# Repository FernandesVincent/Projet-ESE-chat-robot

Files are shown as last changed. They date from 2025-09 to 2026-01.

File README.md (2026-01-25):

# Projet ESE – Chat Robot  

Le projet de Chat Robot développé dans le cadre de la spécialité ESE dirigée par M.Fiack et supervisée par lui et M. Papazogou s'est achevé le vendredi 16 Janvier 2026. 

Nous allons donc revenir ici sur les différents aspects notables du projet, notamment ceux où notre projet s'est détaché des consignes initiales.

Nous allons donc passer en revue les différentes parties du projet en commençant par une partie sur l'organisation du projet et des tâches attribuées aux différents membres de l'équipe puis nous aborderons la partie Hardware séparée en deux sous parties, l'une pour la modélisation 3D sous Onshape et l'autre pour la conception de PCB sous Kicad. Puis, nous aborderons la partie Software séparée en plusieurs parties, chachune abordant un composant important du projet. 

Par soucis de lisibilité de l'ensemble du document nous n'allons pas détaillé en profondeur toutes les parties et sous parties liées à la mise en place de chaque composant sur le PCB ou à leur programmation. À la place, nous expliquerons brièvement l'ensemble des logiques hardware et software pour ensuite analyser en profondeurs seulement certains aspects de ces parties.

## Organisation du Projet

Le projet a été porté par une équipe de quatres étudiants de 3ème année à l'ENSEA faisant partit de la spécialité ESE, cette équipe est composée de : 

- Vincent FERNANDES
- Paul CAILLAUD
- Kelly LUO
- Yimei Xia

Après diverses discussions au cours du semestre, voici comment ont été attribués les rôles concernant le projet : 

- Vincent : PCB, modélisation/impression 3D, Soudure CMS & THT, TOFs, Moteurs, LED, LiDAR, mise en commun du code sous FreeRTOS
- Paul : Modélisation 3D, cablâge, Soudure CMS & THT, Accéléromètre, Moteurs
- Kelly : Lidar
- Yimei : Accéléromètre

Par ailleurs un README relatant l'avancée à mi-parcours (13 Novembre) est disponible dans le dossier Gestion.

## Hardware

### Modélisation 3D

Pour notre projet, nous avons décidés d'utiliser un pack de batteries Li-ion 2S au lieu du pack de 5 batteries NIMH fournit à la base car cela nous apporte une stabilité de maintient de la tension aux bornes de la batterie ainsi qu'une simplicité de la recharge. En effet, pour recharger les batteries que nous utilisions il nous fallait simplement les connecter à n'importe quelle alimentation stabilisée à 8.4V et non pas un chargeur dédié comme pour les batteries NIMH.

Cela étant, dû au fait d'avoir modifier les batteries nous avons dû adapter notre modélisation 3D. Nous avons donc décider d'inclure la pack de batteries directement dans la base du robot comme présenté ci-dessous afin d'augmenter la stabilité de l'ensemble. Cependant, cela a eu pour effet d'augmenter le diamètre de la base de notre robot passant d'une quinzaine de centrimètre à une vingtaine. De plus, nous avons ajouté un cache sur le dessus de la base pour bloquer la batterie en cas de chute ou autre accident. Finalement nous avons également équipé la base d'un arceau afin d'accueillir un bandeau de LED Neopixel ws2812b. 

<figure style="display:flex; gap:5px;">
  <figure style="text-align:center;">
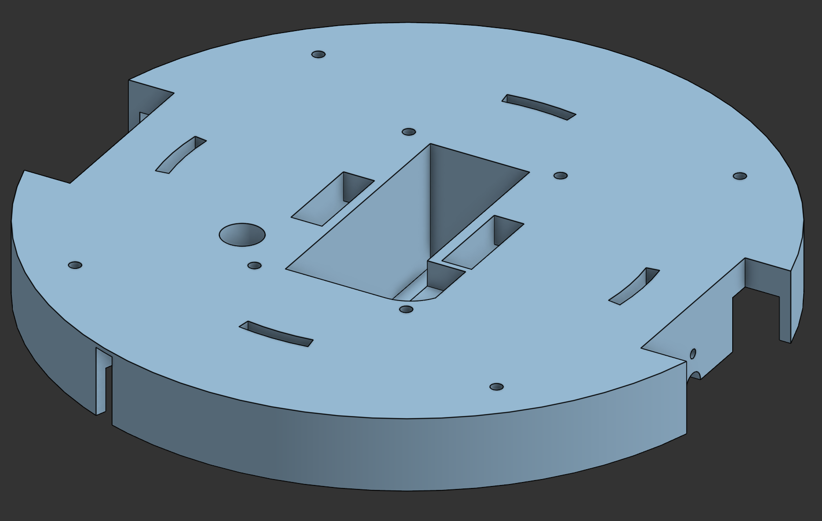
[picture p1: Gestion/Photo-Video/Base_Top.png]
    
    <figcaption>Base vue du dessus</figcaption>
  </figure>
  <figure style="text-align:center;">
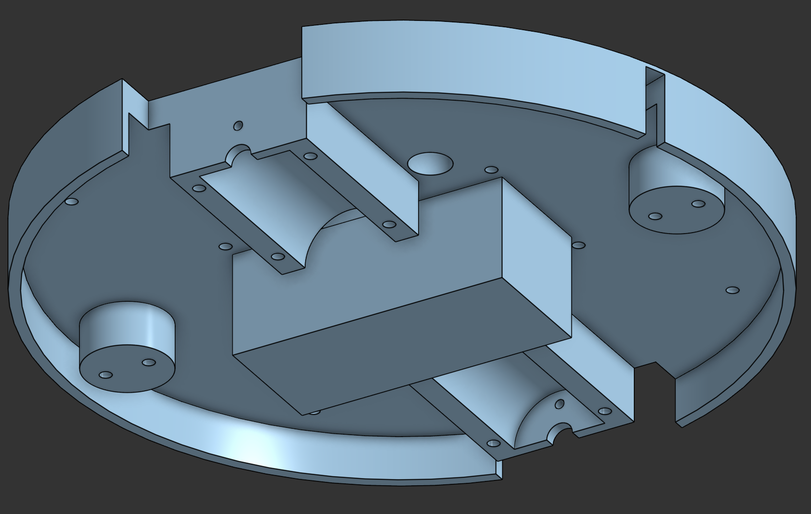
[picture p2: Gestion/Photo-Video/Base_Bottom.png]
    
    <figcaption>Base vue du dessous</figcaption>
  </figure>
</figure>
<figure style="display:flex; gap:5px;">
  <figure style="text-align:center;">
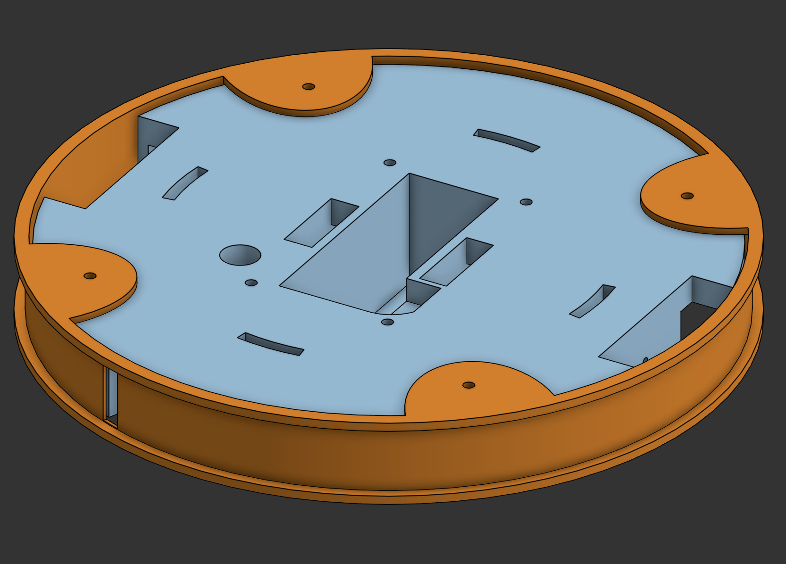
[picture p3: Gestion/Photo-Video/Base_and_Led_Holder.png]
    
    <figcaption>Support de LED</figcaption>
  </figure>
  <figure style="text-align:center;">
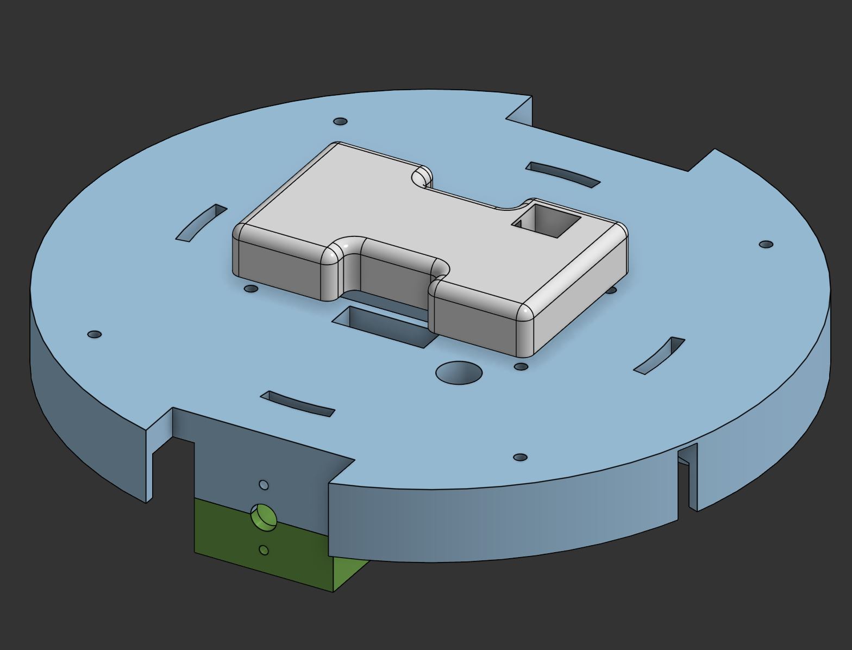
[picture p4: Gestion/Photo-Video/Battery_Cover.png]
    
    <figcaption>Cache de la batterie</figcaption>
  </figure>
</figure>

Contrairement aux autres robots, nous n'avons fait qu'un unique étage, sur lequel sont placé les 6 TOFs et le LiDAR, afin d'avoir la place entre le cache de la batterie et le sol de cet étage de placer le PCB suspendu par des vis M3 et bloqué par les écrous correspondants.

<figure style="display:flex; gap:16px;">
  <figure style="text-align:center;">
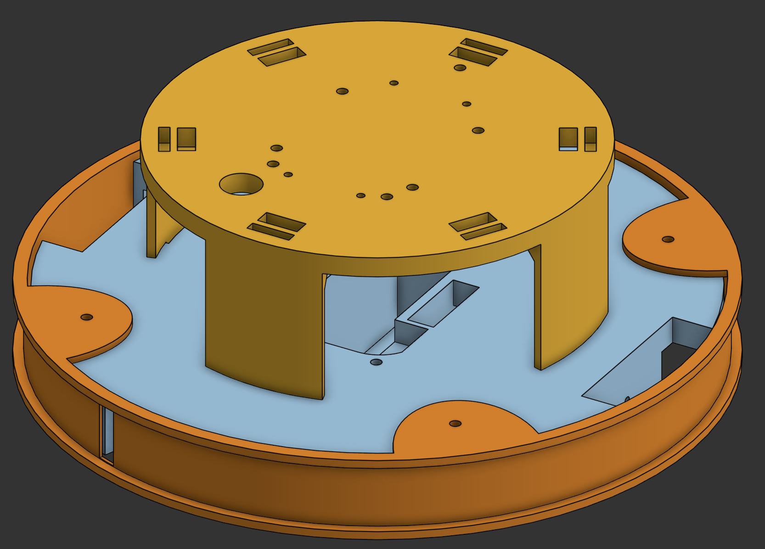
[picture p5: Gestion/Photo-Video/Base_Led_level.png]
    
    <figcaption>Étage du robot</figcaption>
  </figure>
  <figure style="text-align:center;">
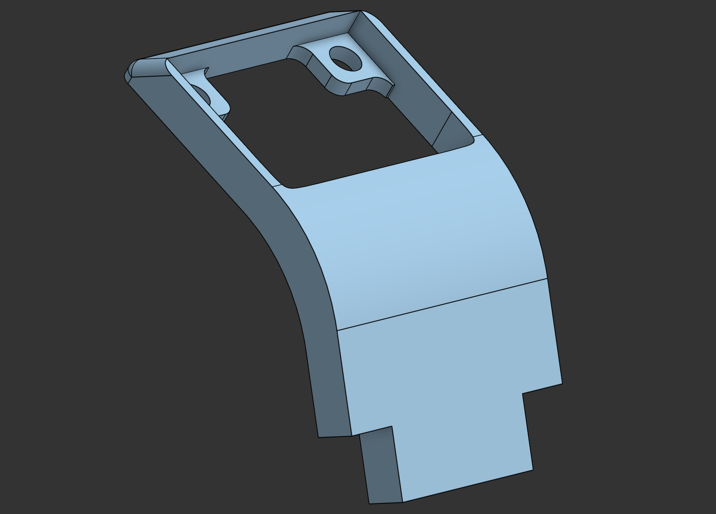
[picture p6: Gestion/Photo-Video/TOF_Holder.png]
    
    <figcaption>Support de TOF</figcaption>
  </figure>
</figure>

De plus, nous avons également modifier les roues afin d'y inclure non pas un mais deux joints toriques par roue afin, encore une fois, de garantir une meilleur stabilité du robot au vu de sa taille. Cependant, cela complexifie légèrement les virages que peut effectuer le robot là où les lignes droites sont cependant meilleures. 
De plus, pour équilibrer le robot nous utilisons des billes en métal dont le support initial accepte uniquement des vis M2 or nous n'avons pas réussi à trouver des vis de ce diamètre assez longues pour être compatible avec notre modélisation. Ainsi, nous avons recréés des supports inspirés des initiaux mais utilisant des vis M3 car nous les avions à la longueur adéquate et à cela s'ajoute qu'utiliser des vis de plus gros diamètre permet de joindre plus solidement les 2 pièces.

<figure style="display:flex; gap:16px;">
  <figure style="text-align:center">
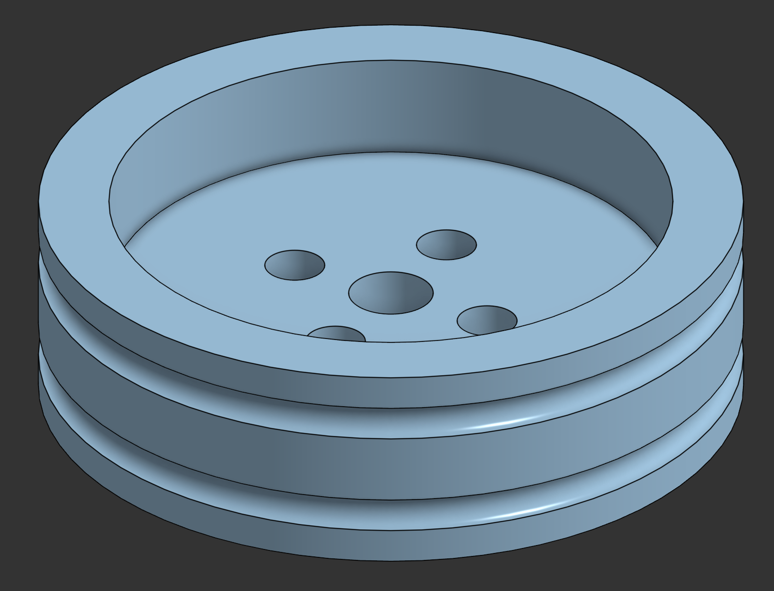
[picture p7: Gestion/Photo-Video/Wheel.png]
    
    <figcaption>Roue</figcaption>
  </figure>
  <figure style="text-align:center">
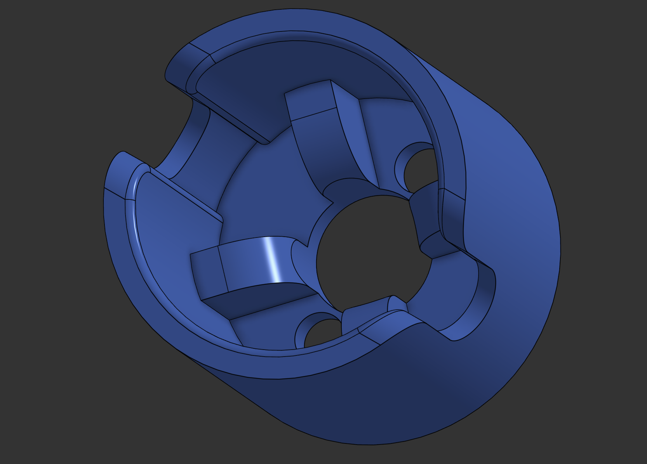
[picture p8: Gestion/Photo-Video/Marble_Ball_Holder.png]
    
    <figcaption>Support de bille</figcaption>
  </figure>
</figure>

### PCB

Pour la conception de PCB nous sommes passés par le logiciel KiCAD et nous en avons créés 4 différents pour certaines raisons que nous expliquerons au fur et à mesure de l'explication générale de chaque PCB.

#### PCB v1

Ce PCB est le premier qui a été designé pour le projet de robot chat. Il inclut notamment les composants de base utiles au bon fonctionnement du robot tel que les drivers de moteurs, l'accéléromètre et les connecteurs pour les TOFs ainsi que celui pour le LiDAR. En effet, pour ce projet nous avons choisis d'utiliser une solution à base de 6 TOFs afin de détecter le vide autour de la table sur laquelle se déplace le robot. Le choix de 6 TOFs a été réfléchis afin d'avoir suffisament de TOFs pour pouvoir repérer le vide peut importe l'orientation du robot au moment d'approcher le bord de table, sans non plus utiliser une quantité non raisonnable de capteurs.

De plus, ce PCB inclut trois nouveaux éléments que l'on a décidé d'ajouter à notre robot. Le premier est un connecteur vers un module MP3 dans le but de jouer un son, défini en amont, à certains moments clés de la présentation. On peut prendre comme exemple le moment où le vide est repéré par un TOF ou bien au moment d'une collision avec un autre robot. 

Le deuxième élément est un bandeau de LED Neopixels commandé par une PWM avec DMA. Le but ici est de venir, tout comme le module MP3, indiquer la réalisation de certaines actions du robot. Par exemple, l'idée principale était d'illuminer une des 96 LEDs du bandeau dès lors que le LiDAR détecte une cible. Certaines LEDs pourraient s'allumer en rouge en direction de cibles non valides alors qu'une LED unique serait allumée en direction de l'objet valide : l'autre robot.

Finalement, le troisième élément est une Raspberry Pi zéro 2W. Nous avons choisis de l'incorporer pour, d'une part, remplacer la connexion bluetooth demandée mais également d'une autre part pour y développer une interface graphique intéractive. Cette dernière permettrait de récupérer les données captées par le robot en temps réel mais également de lui envoyer des instructions, également en temps réel grâce à une lisaion UART.

L'ajout de ces composants nous a obligés à changer le microcontrôleur fourni de base par un STM32G474RET6 possédant, au contraire de l'initial, le nombre suffisant d'HUART accessibles simultanément pour nos besoins.

<figure style="display:flex; gap:16px;">
  <figure style="text-align:center">
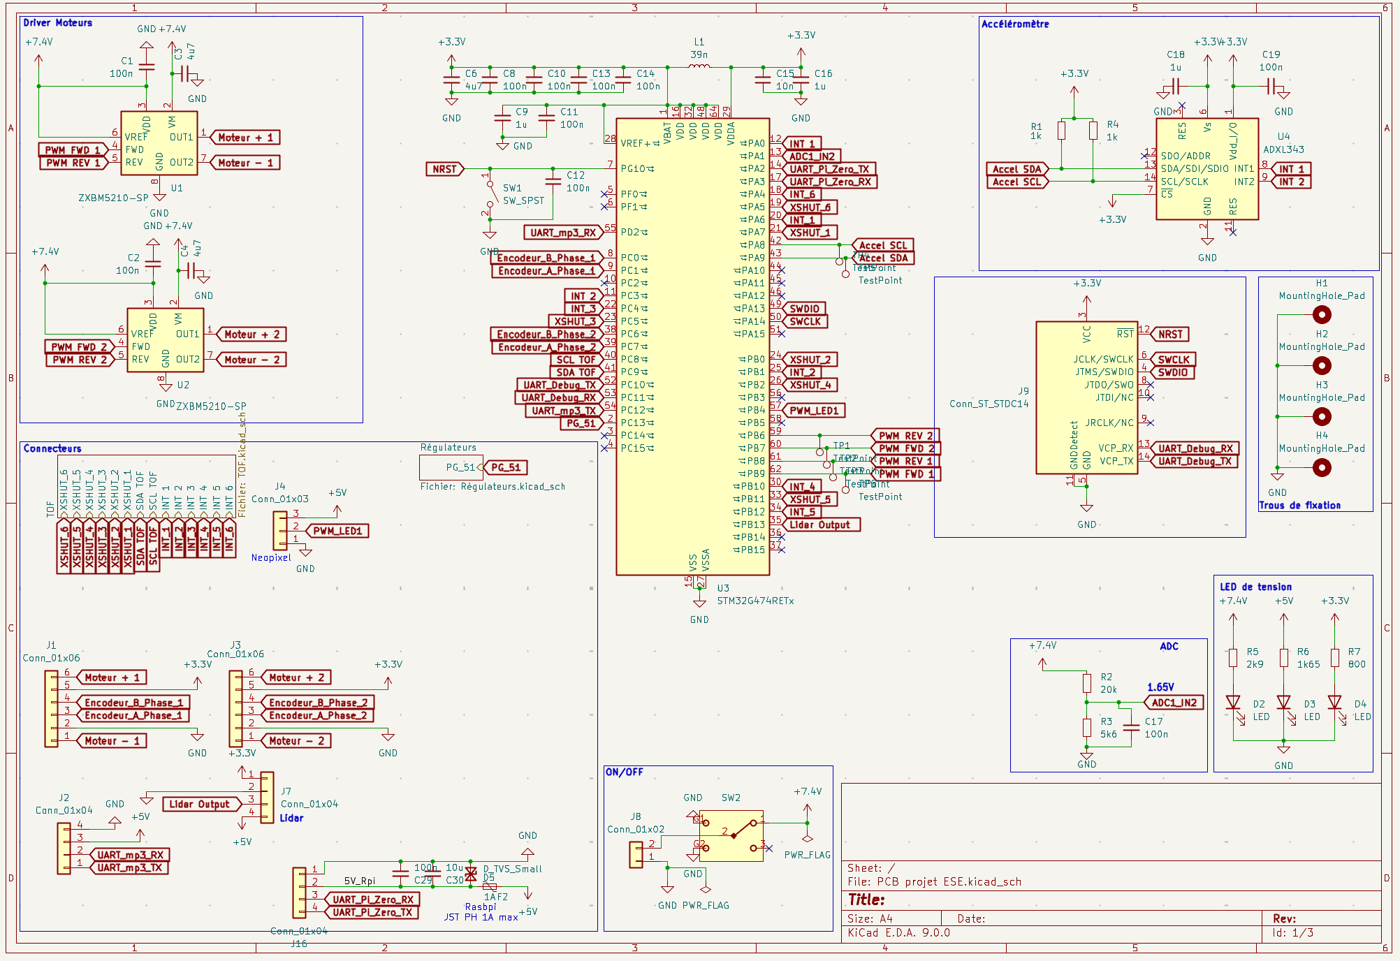
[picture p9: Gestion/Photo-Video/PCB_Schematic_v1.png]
    
    <figcaption>Schematic</figcaption>
  </figure>
  <figure style="text-align:center">
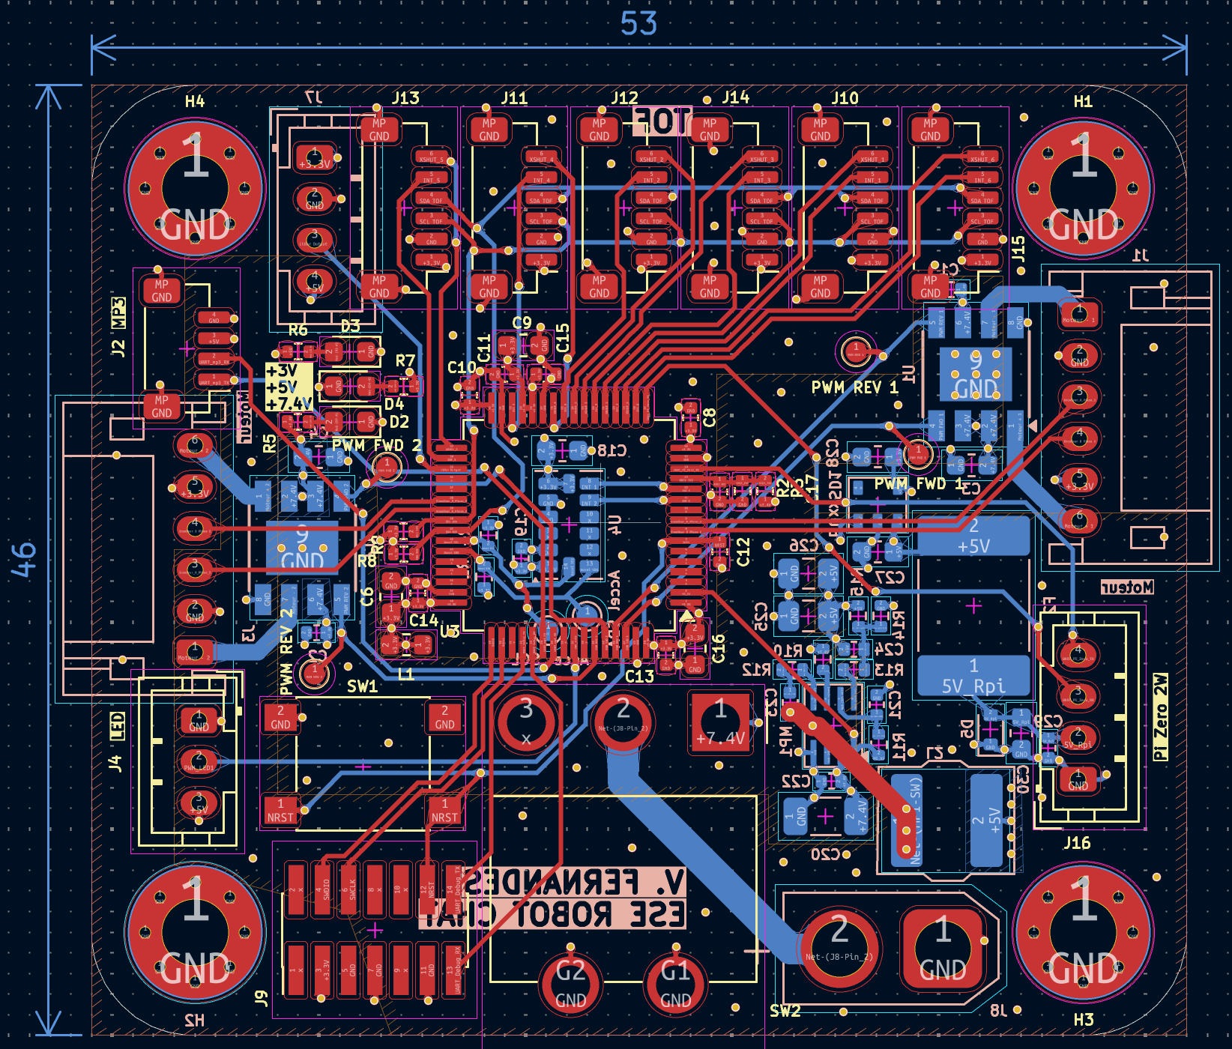
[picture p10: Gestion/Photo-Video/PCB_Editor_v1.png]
    
    <figcaption>PCB Editor</figcaption>
  </figure>
</figure>

Cependant, plusieurs problèmes datant de la conception sous KiCAD sont apparus une fois le PCB soudé et testé. Parmi celles-ci, les plus notables et plus importante sont les suivantes : 

- Oubli de connection de la pin ADDR de l'accéléromètre à GND (ou VCC en fonctiond de l'adresse voulue).
- Inversion des connexions SDA/SCL pour l'I2C de l'accéléromètre.
- Mauvaise connexion du pin Tx du LiDAR à un GPIO simple.
- Mauvaises connexions des pins GPIO des TOFs empêchant leur utilisation en interruption.

Même si, à la fin du projet nous avons pu en partie corriger ces erreurs de différentes façons il nous semblait essentiel de les faire apparaître dans ce compte rendu. Par exemple, nous avons connectés le LiDAR au connecteur de la Pi qui utilise également un UART et nous avons utilisés les TOFs en polling et non en interruption.

#### PCB v1.5

Cette version du PCB a été créée suite à la découverte des erreurs présentes sur la première version. Cette version a été designée dans l'idée d'avoir un PCB purement fonctionnel corrigeant les erreurs du PCB précédent tout en enlevant les éléments non nécessaires ajoutés dans la v1. Nous avons tout de même gardé le même microcontrôleur STM32G474RET6 bien que le nombre de pins soit bien plus important que nécessaire car cela nous a permis de gagné du temps en conception et le PCB a donc pu être réalisé en moins d'une journée.

<figure style="display:flex; gap:16px;">
  <figure style="text-align:center">
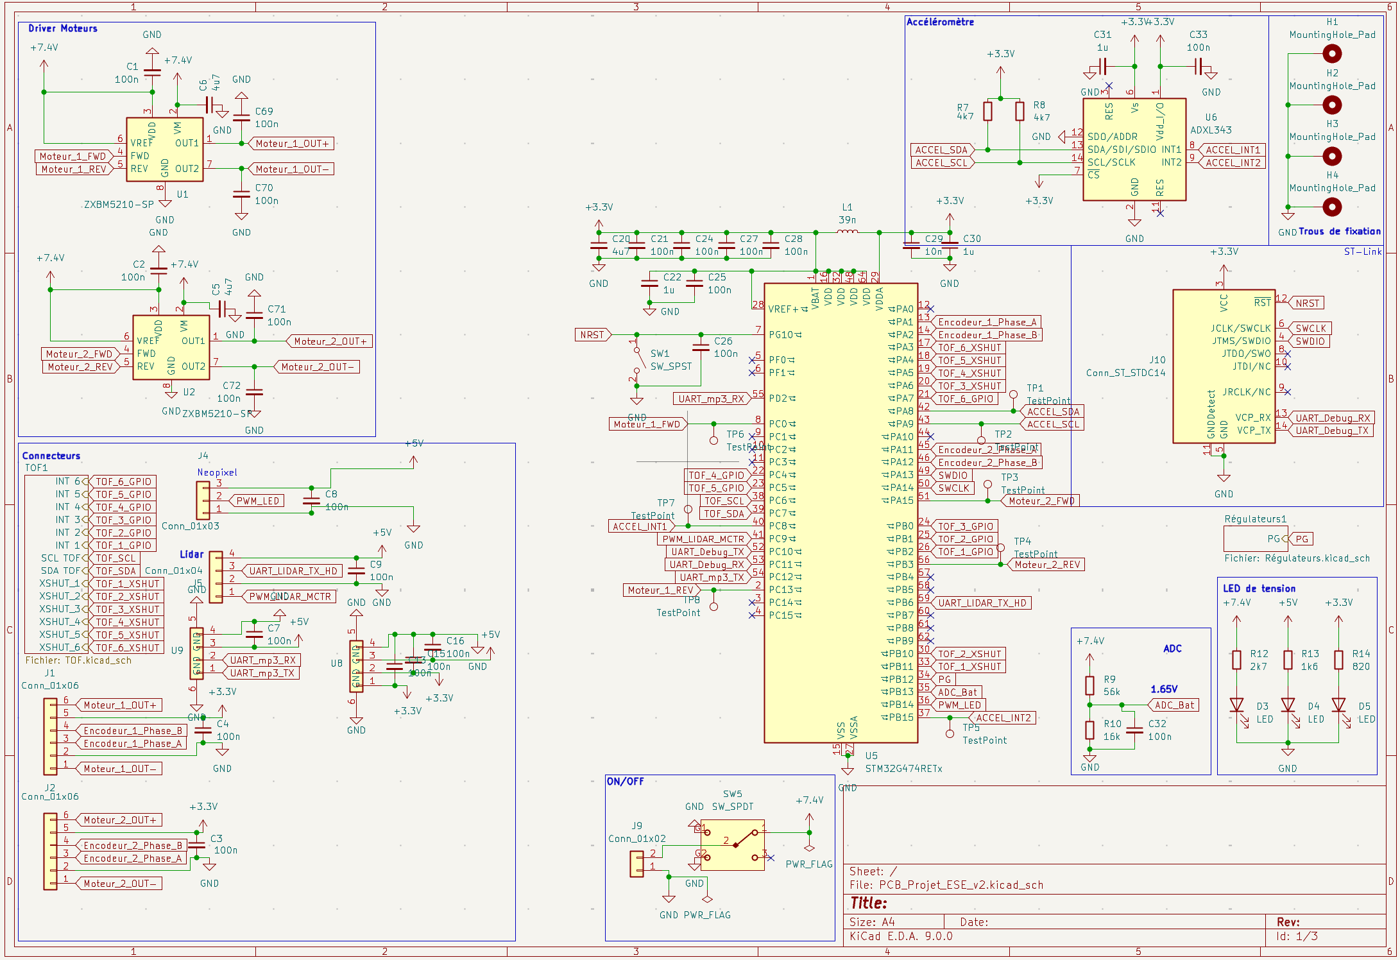
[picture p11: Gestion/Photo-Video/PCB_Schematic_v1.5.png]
    
    <figcaption>Schematic</figcaption>
  </figure>
  <figure style="text-align:center">
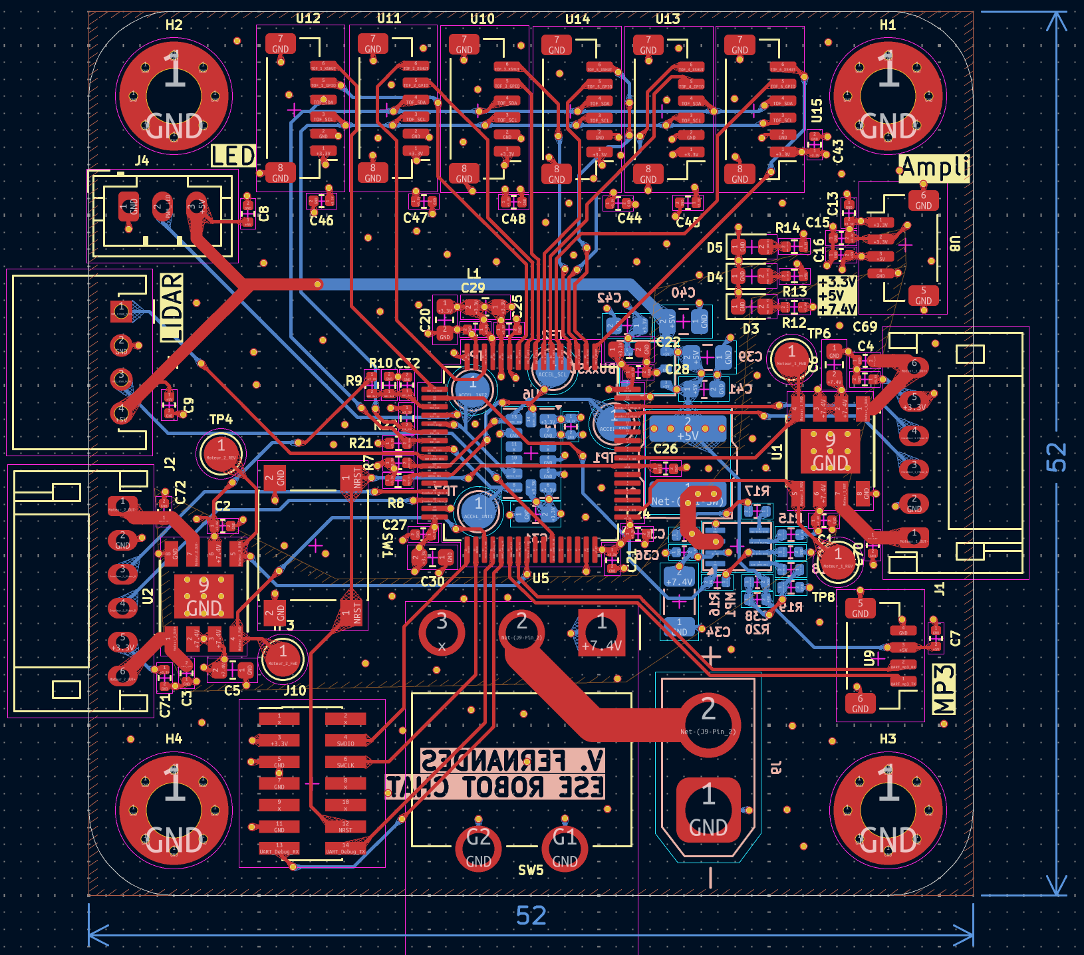
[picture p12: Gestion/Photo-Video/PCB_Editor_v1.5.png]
    
    <figcaption>PCB Editor</figcaption>
  </figure>
</figure>

Malheureusement, cette version a seulement eu le temps d'arrivée pour le jour exact de la présentation du projet car il y a eu de nombreuses semaines de retard dans la validation finale de la commande contenant ce PCB par le service déidé de l'établissement auprès du fabricant. 

#### PCB v2

Cette version est une version plus avancée du premier PCB, plus petite et comportant plus de composants et fonctionnalités. Parmi tout ces ajouts, les plus sont notables sont l'ajout d'un système de visualisation de la batterie en analogique uniquement, de résistances de shunt associées avec des amplificateurs afin de pouvoir asservir les moteurs en courant. De plus, des connecteurs pour utiliser pleinement le PCB dédié à l'amplificateur audio ainsi qu'un bouton ON-OFF-ON utilisé pour choisir le mode du robot ont été ajoutés au PCB.

<figure style="display:flex; gap:16px;">
  <figure style="text-align:center">
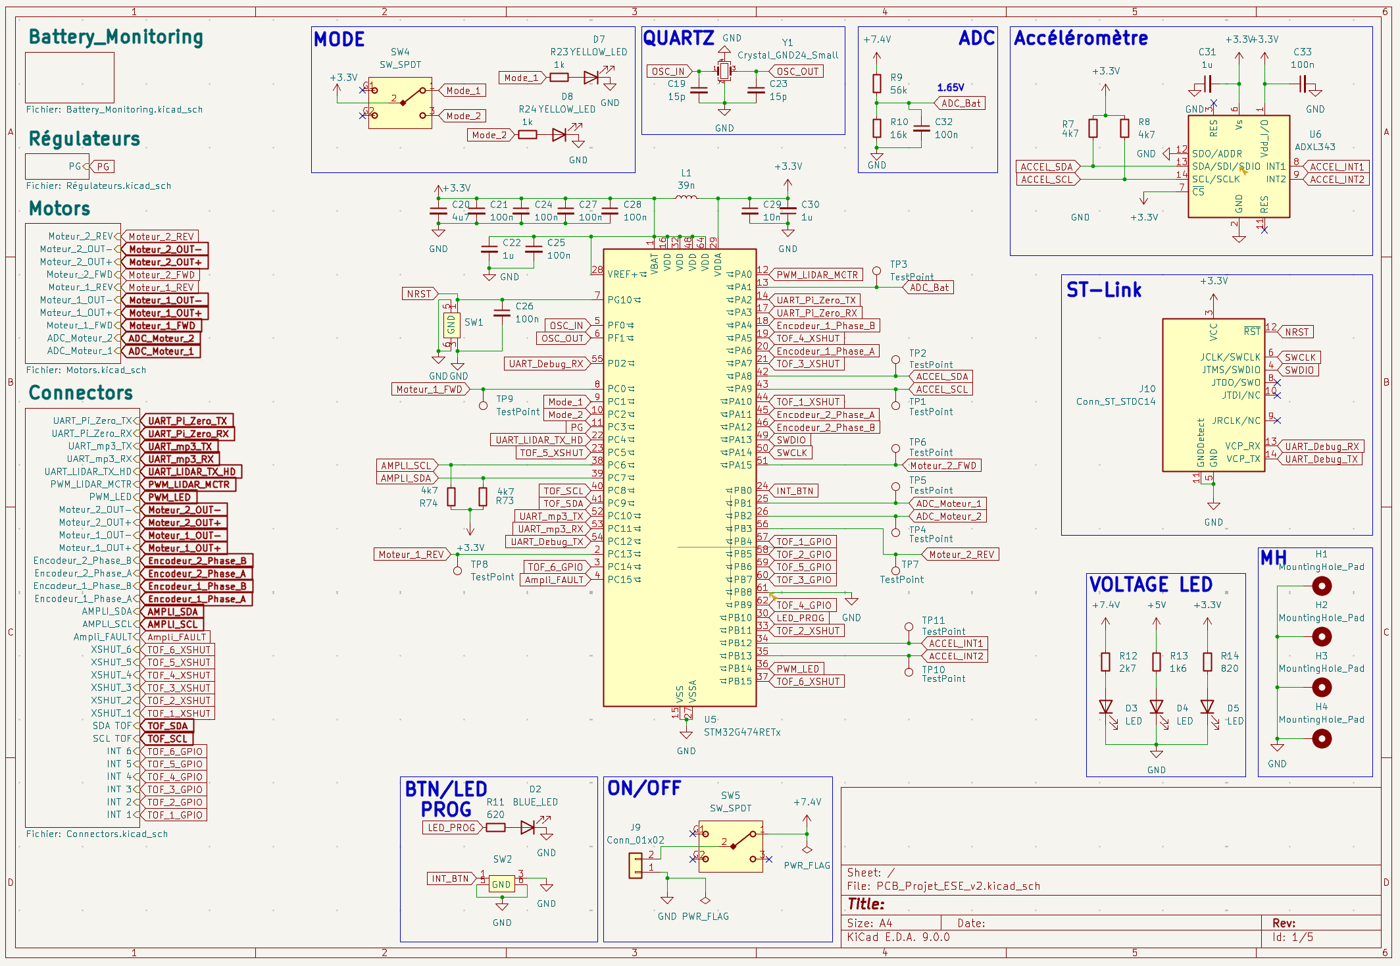
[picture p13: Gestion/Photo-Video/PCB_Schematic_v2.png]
    
    <figcaption>Schematic</figcaption>
  </figure>
</figure>

<figure style="display:flex; gap:16px;">
  <figure style="text-align:center">
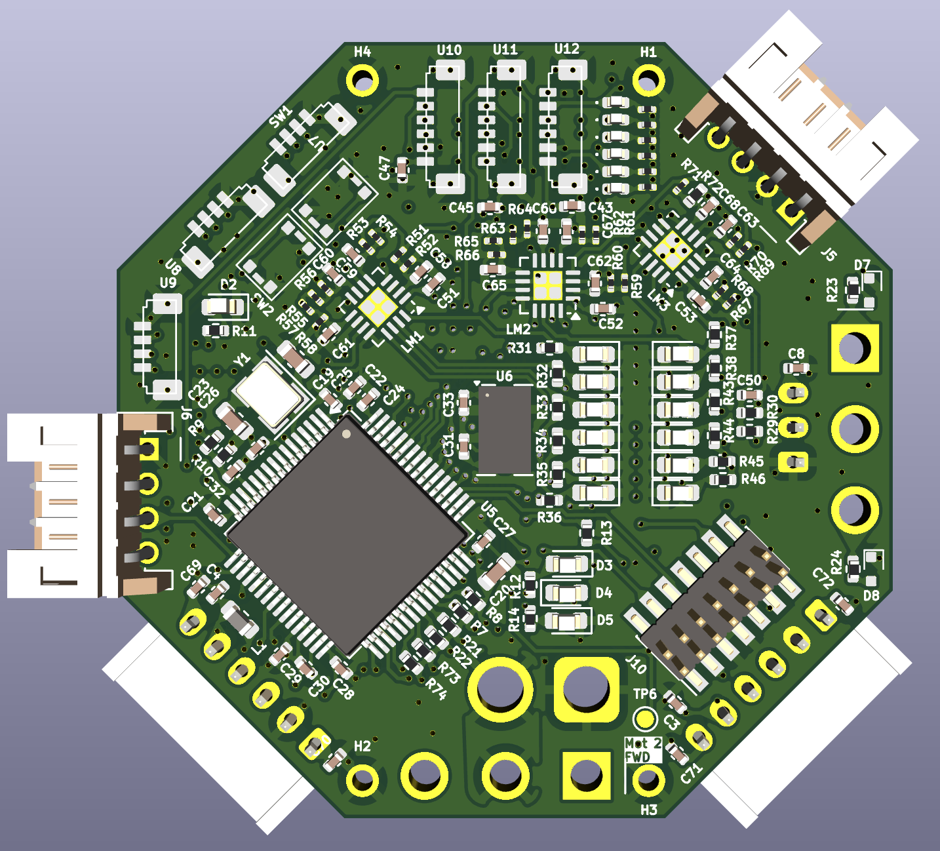
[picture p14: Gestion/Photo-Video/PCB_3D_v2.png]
    
    <figcaption>Vue 3D Top</figcaption>
  </figure>
  <figure style="text-align:center">
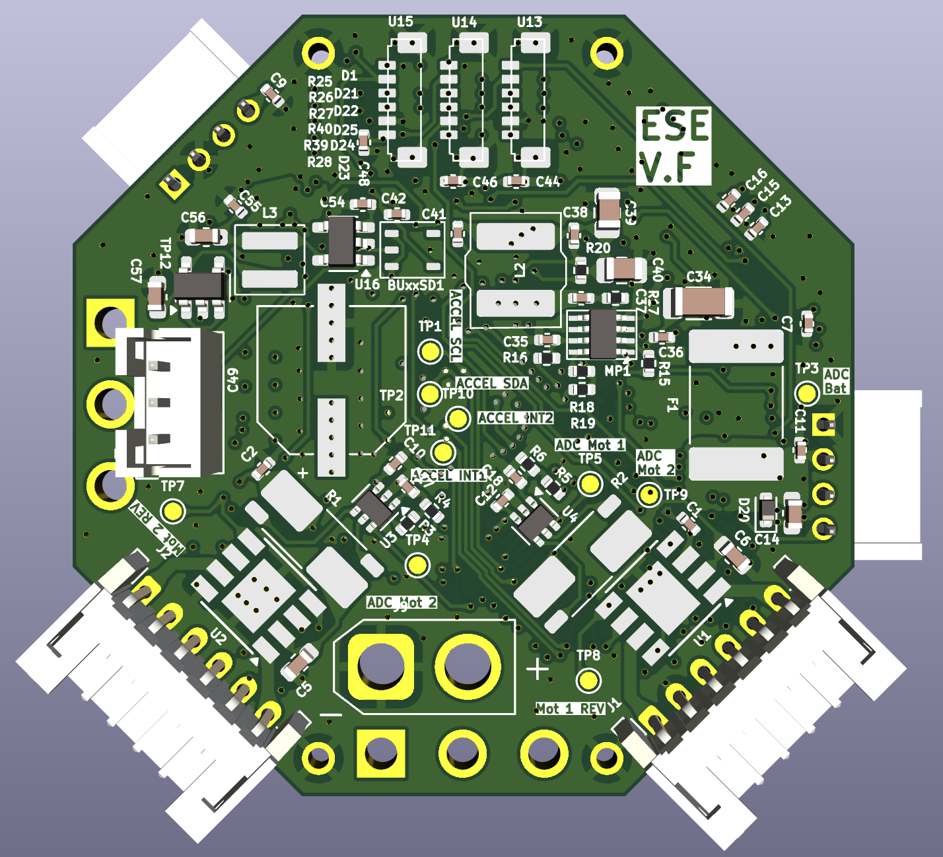
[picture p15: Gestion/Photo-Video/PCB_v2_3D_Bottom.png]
    
    <figcaption>Vue 3D Bottom</figcaption>
  </figure>
</figure>
  
Pour créer le système de surveillance de la batterie, des comparateurs LM339LVRTER ont été utilisés pour comparer la tension réelle de la batterie à une tension de référence qui ne varie pas même si la tension de la batterie diminue. Cette tension de référence a été créée par la mise en série d'un abaisseur de tension (MCP1802T-0902I/OT) permettant une sortie de tension de 0.9V tant que la tension d'entrée est supérieure à 2V et d'un amplificateur de tension (TPS61097A-33DBVR) permettant de ramener la tension à 3.3V qui est donc comparable à la tension réelle passée dans un diviseur de tension. Un module Buck-Boost aurait pu remplacer cette mise en série des deux composants mais nous n'en avons pas trouver permettant d'avoir ces valeurs de tension de manière stable même lorsque la tension réelle approche les 2V. 
Pour afficher le niveau de la batterie un jeu de 12 LEDs CMS a été installé sur le PCB, tant que la tension réelle est supérieure à la tension seuille, la LED associée est allumée mais dès lors que le tension réelle est inférieure à la tension seuille la LED s'éteint. Dans un soucis uniquement visuel les 12 LEDs forment un dégradé allant de vert à rouge.

Malheureusement, cette version a seulement pu être soudée (non testée) avant la présentation du projet car il y a eu de nombreuses semaines de retard dans la validation finale de la commande contenant ce PCB par le service déidé de l'établissement auprès du fabricant. 

#### PCB audio

Ce PCB très simple utilise uniquement un amplificateur audio (LM48100QMHX/NOPB) afin d'amplifier le signal en sortie du module MP3. Ce dernier utilise un câble mini-jack fonctionnant pour une utilisation en connexion directe comme avec un casque audio. Cependant cette sortie mini-jack ne fournit pas assez de puissance pour qu'un haut parleur directement connecté à celle-ci produise un son audible. Il faut donc, entre le haut-parleur et le module MP3, ajouter un amplificateur audio. 

<figure style="display:flex; gap:16px;">
  <figure style="text-align:center">
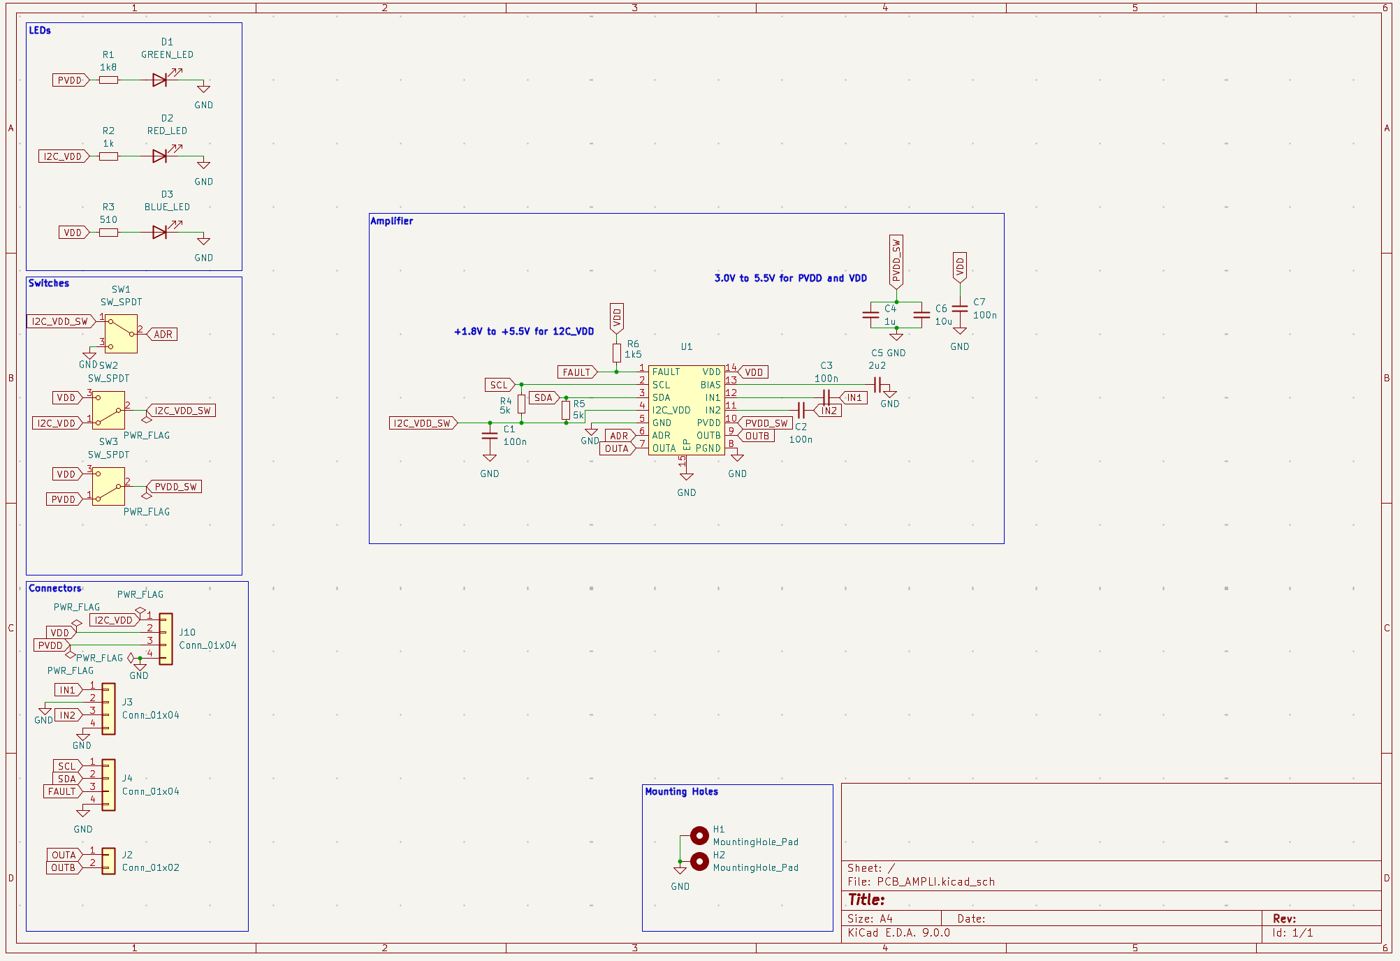
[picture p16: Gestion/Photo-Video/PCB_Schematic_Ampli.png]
    
    <figcaption>Schematic</figcaption>
  </figure>
  <figure style="text-align:center">
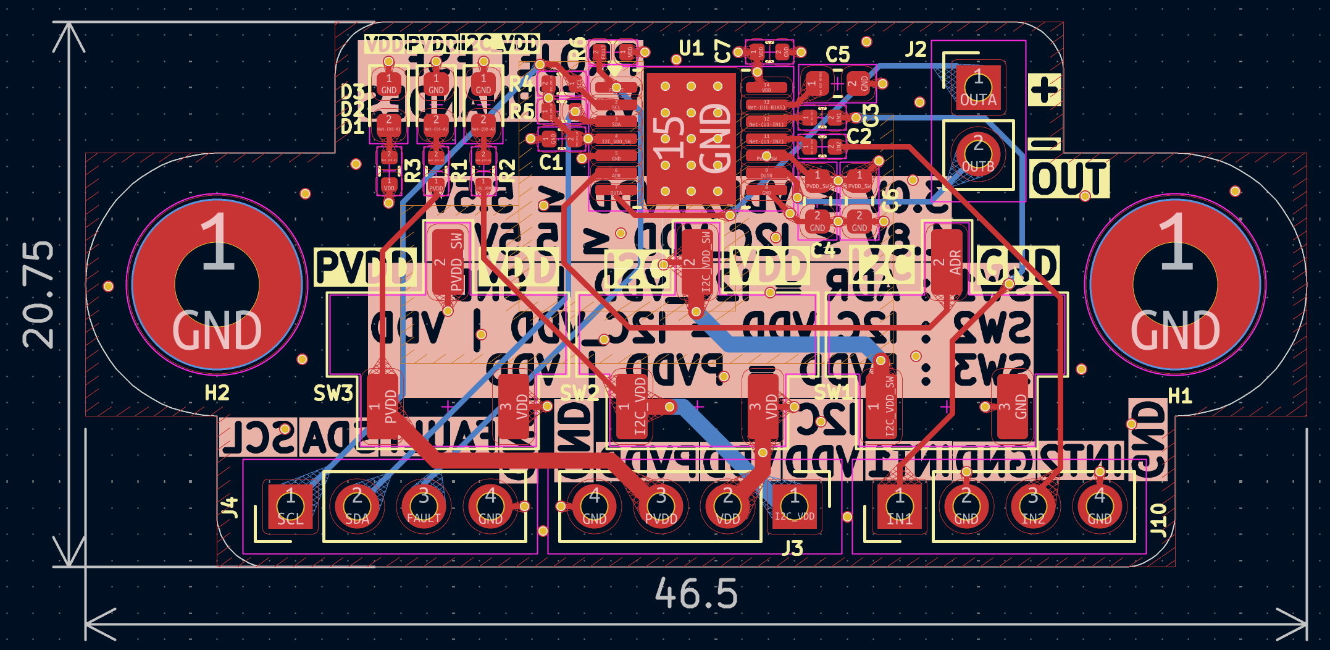
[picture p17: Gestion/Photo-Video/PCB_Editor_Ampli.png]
    
    <figcaption>PCB Editor</figcaption>
  </figure>
</figure>

Cet amplificateur audio a été choisi, tout d'abord pour ses spécificités techniques de 1W/8ohms correspondant excatement à celles de notre haut-parleur. De plus, quand la liste des choix possibles a été suffisament réduite nous avons pris le parti de choisir celui de la marque Texas Instrument car leur documentation est très lisible et compréhensible comparée à celle de leur concurrent. Cela nous permet, par exemple, de réduire le temps passé tant sur la partie hardware que sur la partie software de ce PCB. De plus, La communication I2C de cet l'amplificateur permet de modifier le volume en sortie sur 28 niveaux différents, ce qui est encore un autre avantage de ce dernier. Le seul "inconvénient", s'il faut en citer un, est le fait que le composant soit de base dans un état de veille et qu'il doit être "réveillé" grâce à l'écriture dans l'un de ses registres via la communication I2C, ce qui oblige à toujours devoir le connecté en I2C pour qu'il fonctionne.

## Software 

Des précisions supplémentaires pour les parties de Kelly LUO sont disponibles [ici](/software/README.md).

### LiDAR

Le LiDAR est l'élément qui permet au robot de :
- détecter la cible à pourchasser lorsque le robot est en mode chat.
- détecter la cible à fuir lorsque le robot est en mode souris.

Le YDLIDAR X2, fournit et imposé, communique en liaison UART avec le MCU du PCB. Comme il n'a qu'une seule broche Tx pour cette liaison, nous avons décidé de réglé l'UART en mode Half-Duplex car comme nous ne faisons que recevoir des données il n'est pas nécessaire d'avoir une liaison utilisant Tx et Rx.

Ce LiDAR transmet 3000 trames, chacune contenant plusieurs points, par seconde et effectue entre 5 et 8 tours par secondes en fonction de la tension (ou PWM) appliquée sur le pin M_CTR du LiDAR. Pour avoir une meilleure précision nous avons préférés travailler avec une vitesse entre 6 et 8 tours par secondes.

Le code associé au LiDAR est disponible en 2 versions, l'un créée par Kelly LUO est fonctionnelle sur la nucleo-L476RG mais pas sur le MCU du projet et est disponible dans le dossier : "lidar_nucleo". La seconde version créée par Vincent FERNANDES est adaptée au MCU du projet mais n'a pas pu être finie à temps pour la présentation du projet.

Ci-dessous, les explications du code de la première version par Kelly LUO : 
  
La YDLIDAR X2 est interfacé en UART avec notre micro controleur et les données envoyés suit un protocole particulier.
Pour atteindre notre objectif, il nous a d'abord fallut traiter les informations reçu. Les trames reçu comportais beaucoup de valeur nulle, qui ne correspondait pas à un distance nulle, mais plus à un signal envoyé et non reçu. Nous avons décider de stocker les distances de plusieurs trames, pour avoir une image de l'environnement plus complète. Ensuite, nous avons mis en place un algorithme de détection de cible. L'algorithme mis en place est assez précis, mais je pense qu'il est lourd en calcul. Peut être qu'un algorithme plus simple aurait été plus adapté pour notre utilisation.

Ci-dessous, les explications du code de la seconde version par Vincent FERNANDES : 

L'objectif est ici de repérer une cible déterminée comme valide et d'agir en conséquence en fonction du mode (chat ou souris) dans lequel se trouve le robot. 

Pour effectuer ce travail, nous avons choisis d'analyser tour par tour ce que percevait le LiDAR. Pour ce faire nous surveillons un bit précis du protocole du LiDAR qui est à 1 lorsque qu'un nouveau tour est entammé.

Pour chaque tour nous traitons les trames et en récupérons l'ensemble des points ayant chacun les attributs "distance" et "angle", ce qui nous permet de "dessiner" un cercle de ce que perçoit le LiDAR à chacun de ces tours. 

Afin d'éviter d'inclure des distances éronnées dans ce cercle nous limitons la distance maximale tel que si la distance d'un point est perçue supérieure à celle-ci alors nous lui attribuons pour valeur celle de la distance maximale choisie. 

Pour déterminer le nombre d'objets et leur position respectives nous utilisons l'algorithme suivant : 

1. Dans une boucle allant du premier au dernier point du cercle, choisir un point i.
2. Comparer la valeur de distance de ce point i à un seuil.
3. Si la distance du point i est inférieure au seuil alors faire de même pour les 4 points suivants, moyenner et comparer la moyenne au seuil sinon passer au point suivant.
4. Si la valeur moyennée est également inférieure au seuil alors enregistrer le point i comme premier point de l'objet j puis enregistrer tout les points qui suivent comme faisant partis de l'objet jusqu'à ce qu'un point i+n contredisant l'étape 3 apparaisse, ce point est alors enregistrer comme le point de fin de l'objet.
5. Répeter cette boucle pour tout les points du cercle.
6. Pour chaque objet enregistré, déterminer le diamètre réel de celui-ci grâce aux équations d'Al-Kashi.
7. Si le diamètre calculé est égal à un diamètre prédéfinis avec une certaine incertitude alors l'objet est considéré comme valide sinon il est considéré comme ne l'étant pas.
8. Pour l'objet valide, récupérer le point de l'objet ayant la distance la plus courte au LiDAR.
9. Diriger le robot en direction de l'angle associé au point récupérer à l'étape précédente.
10. Si plusieurs objets sont valides, calculer la distance moyenne de leurs points et se diriger vers le point de l'étape 8 pour l'objet ayant la moyenne de distance la plus basse.
11. À la fin du traitement du tour, vider l'ensemble des buffers puis recommencer.

Cet algorithme est assez lourd mais cela ne pose pas de problème majeur dans notre cas particulier car le STM32G474RET6 possède suffisament de RAM pour le traiter. Avec plus de temps, un algorithme plus léger aurait surement pu être trouvé.

### Moteurs

Les moteurs sont un élement essentiel du projet puisqu'il faut que le robot puisse se déplacer sur la table. Nous avons à notre disposition des moteurs FIT0520 qui seront chacuns pilotés par un driver. Nous avons fait le choix de faire une structure par moteur, cette dernière contenant le timer qui correspond à la PWM qui sera appliquée, la direction (Forward ou Reverse), la vitesse ainsi que le channel pour le timer. Un deuxième type de structure a ensuite été créé, celle du PID qui contient les valeurs des coefficients du correcteur afin de bien asservir le moteur. Il faut cependant noter que nous n'avons pas eu le temps de bien mettre en place le correcteur, les valeures ne sont donc pas les bonnes. Nous avons ensuite eu l'idée d'une autre structure appelée Robot qui comprend les deux moteurs et les PID, nous ne nous en sommes au final pas servis car nous controlions chaque moteur séparément.

<figure style="display:flex; gap:16px;">
  <figure style="text-align:center">
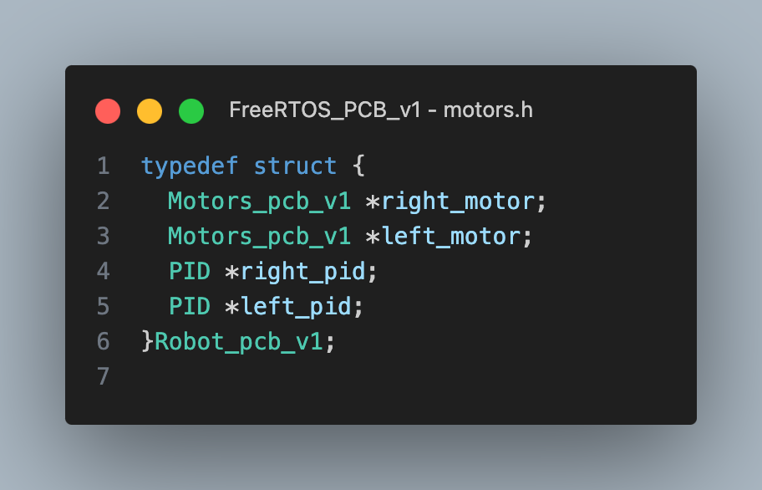
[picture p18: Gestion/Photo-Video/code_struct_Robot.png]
    
    <figcaption>Structure du Robot</figcaption>
  </figure>
  <figure style="text-align:center">
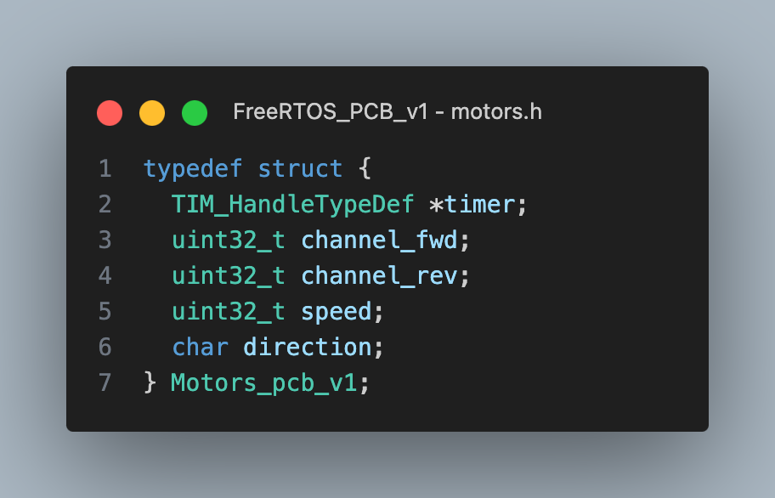
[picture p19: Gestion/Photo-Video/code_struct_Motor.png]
    
    <figcaption>Structure d'un moteur</figcaption>
  </figure>
  <figure style="text-align:center">
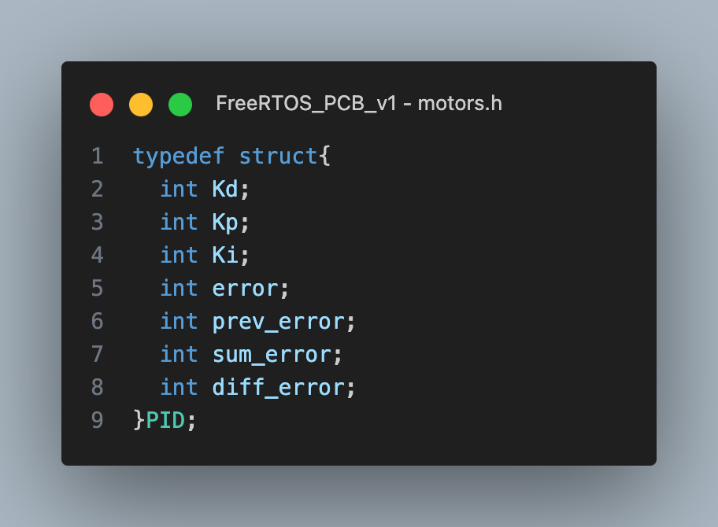
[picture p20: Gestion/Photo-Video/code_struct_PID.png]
    
    <figcaption>Structure du PID</figcaption>
  </figure>
</figure>

Dans le .c, on commence par initialiser chaque moteur, en fournissant le timer ainsi qu'un channel pour "Forward" et un autre pour "Reverse", une vitesse nulle et la direction Forward. (On retrouve aussi les initialisations des autres structures).
Il a ensuite fallu réaliser les différentes fonctions des moteurs, start, stop, ainsi que les changements de direction et les changements de vitesse. En exemple, pour la fonction moteur_forward, le code commence par vérifier quel moteur appelle la fonction, ensuite la PWM correspondante au bon moteur Forward est démarrée. La direction Reverse est éteinte, et ce même si le moteur était arrété précédement.

<figure style="display:flex; gap:16px;">
  <figure style="text-align:center">
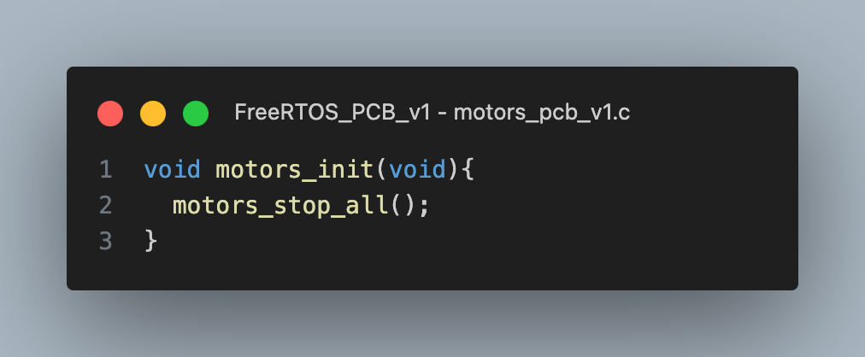
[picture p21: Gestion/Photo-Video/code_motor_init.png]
    
    <figcaption>Fonction d'initialisation</figcaption>
  </figure>
  <figure style="text-align:center">
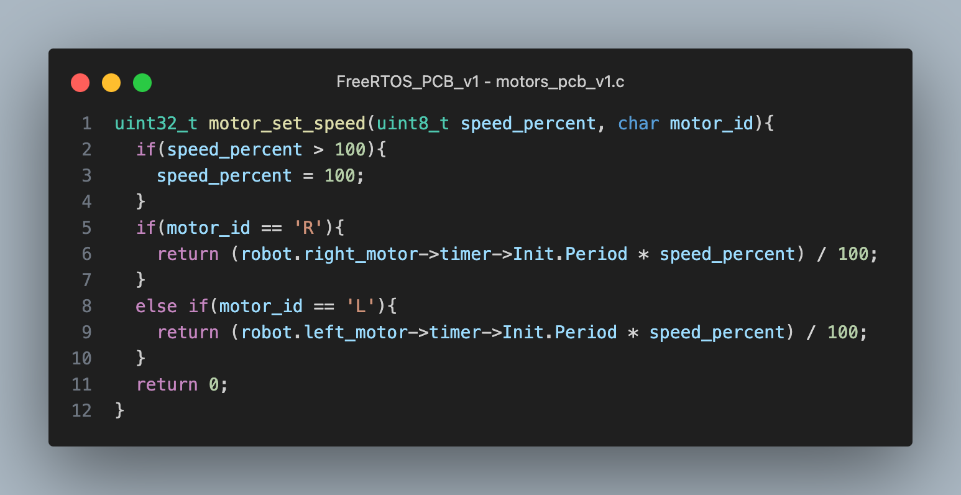
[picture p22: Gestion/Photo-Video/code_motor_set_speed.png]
    
    <figcaption>Fonction de choix de la vitesse</figcaption>
  </figure>
  <figure style="text-align:center">
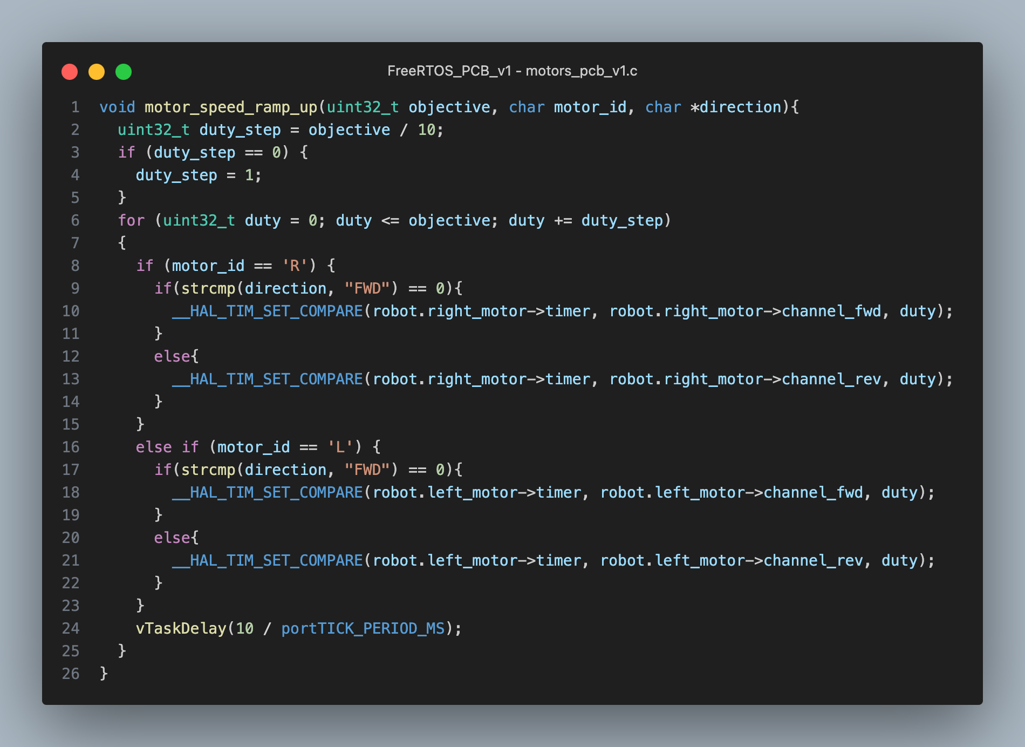
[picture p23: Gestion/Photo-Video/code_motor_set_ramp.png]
    
    <figcaption>Fonction rampe de vitesse</figcaption>
  </figure>
</figure>

<figure style="display:flex; gap:16px;">
  <figure style="text-align:center">
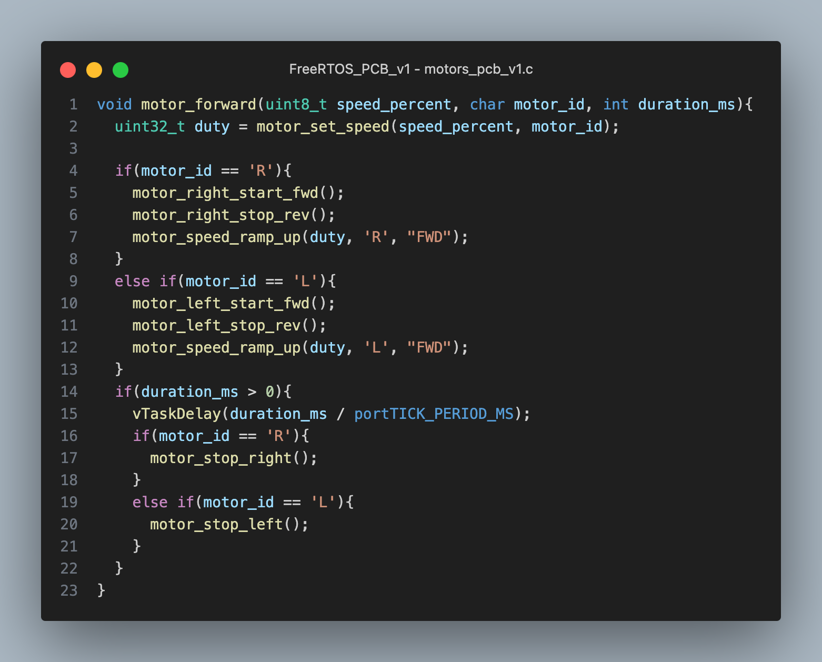
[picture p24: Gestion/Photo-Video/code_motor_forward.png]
    
    <figcaption>Fonction pour avancer</figcaption>
  </figure>
  <figure style="text-align:center">
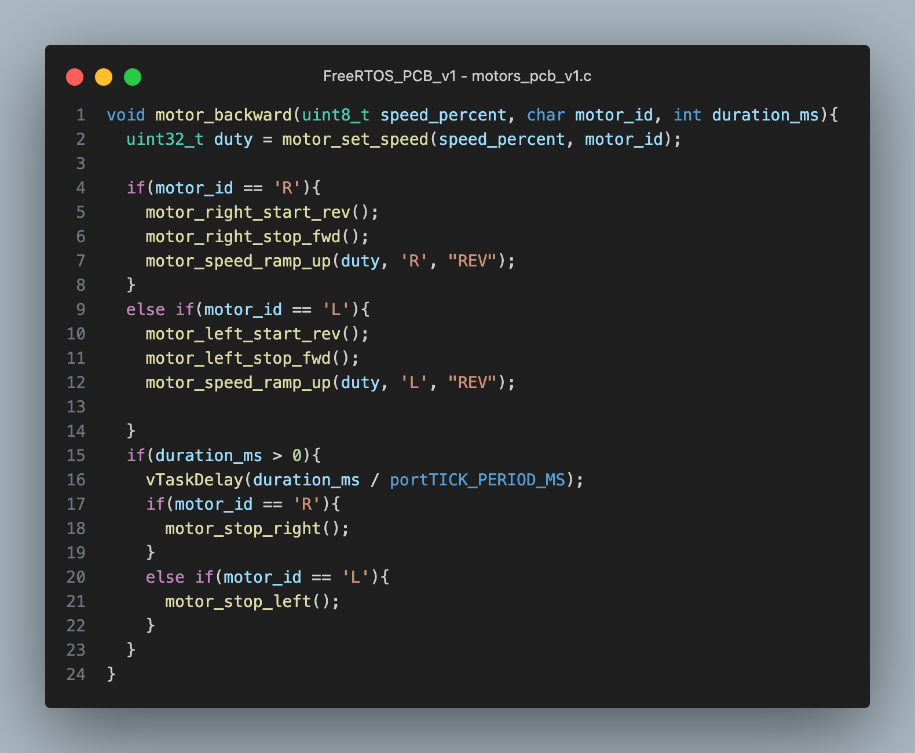
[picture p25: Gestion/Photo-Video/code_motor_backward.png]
    
    <figcaption>Fonction de recul</figcaption>
  </figure>
  <figure style="text-align:center">
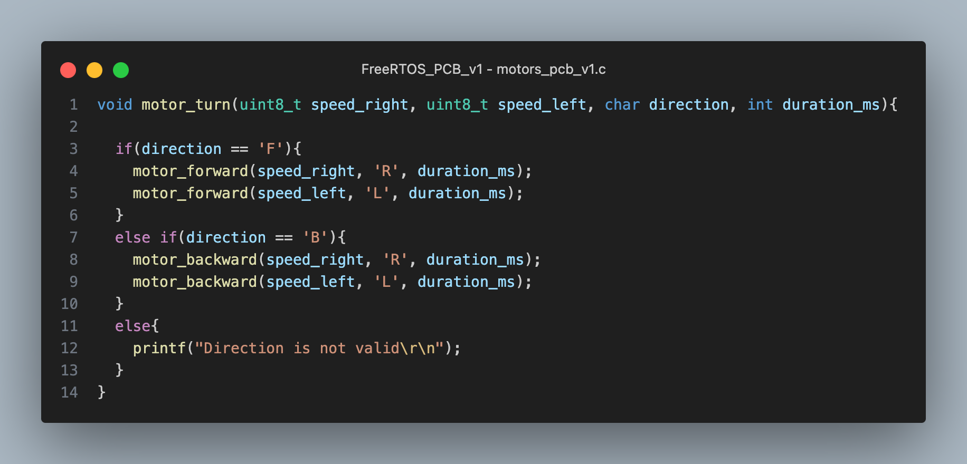
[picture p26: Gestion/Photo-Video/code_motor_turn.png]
    
    <figcaption>Fonction pour tourner</figcaption>
  </figure>
</figure>

### TOF

Pour ce projet, nous utilisons 6 TOFs VL53L0X. Comme notre MCU possède un nombre de pins suffisants nous n'avons pas eu besoin de passer par un multiplexeur I2C pour travailler indépendamment avec chacun des six TOFs. En effet, dans la plupart des cas un multiplexeur est utilisé car ces TOFs ont une adresse fixe identique qui peut être modifiée mais nécessite une ligne supplémentaire par TOF pour connecter le pin XSHUT permettant de mettre en veille ou de reveillé un TOF. En effet, avant toute chose, pour travailler avec les 6 TOFs nous avons besoin de les initialisés avec chacun une adresses différente, pour ce faire nous utilisons les fonctions suivantes : 

<figure style="display:flex; gap:16px;">
  <figure style="text-align:center">
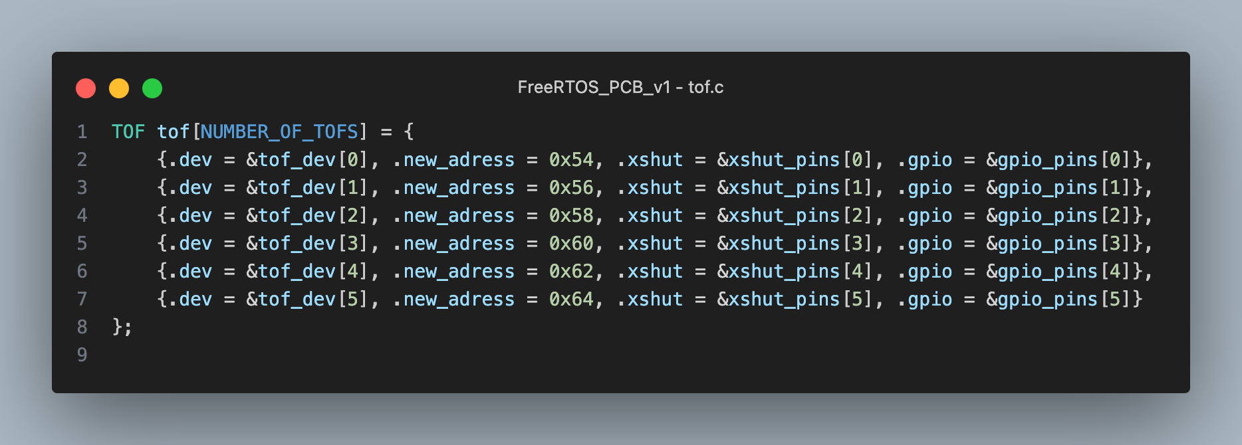
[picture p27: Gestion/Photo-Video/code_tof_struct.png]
    
    <figcaption>Structure des nouvelles adresses des TOFs</figcaption>
  </figure>
  <figure style="text-align:center">
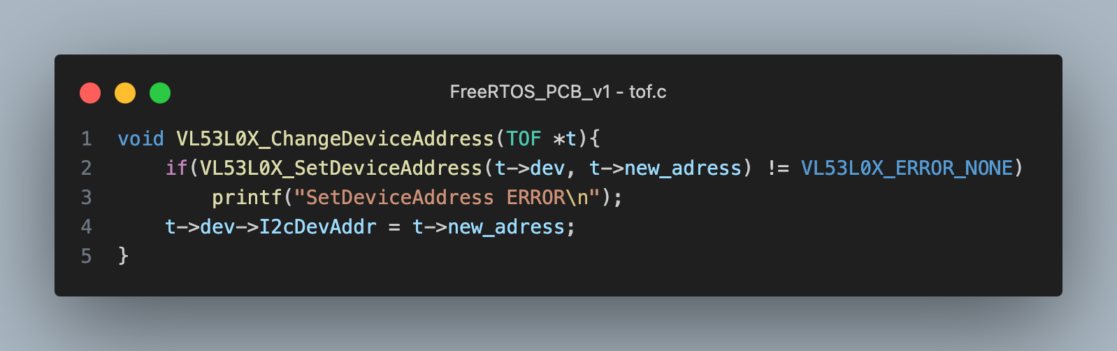
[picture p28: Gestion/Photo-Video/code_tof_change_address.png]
    
    <figcaption>Fonction de changement d'adresse</figcaption>
  </figure>
  <figure style="text-align:center">
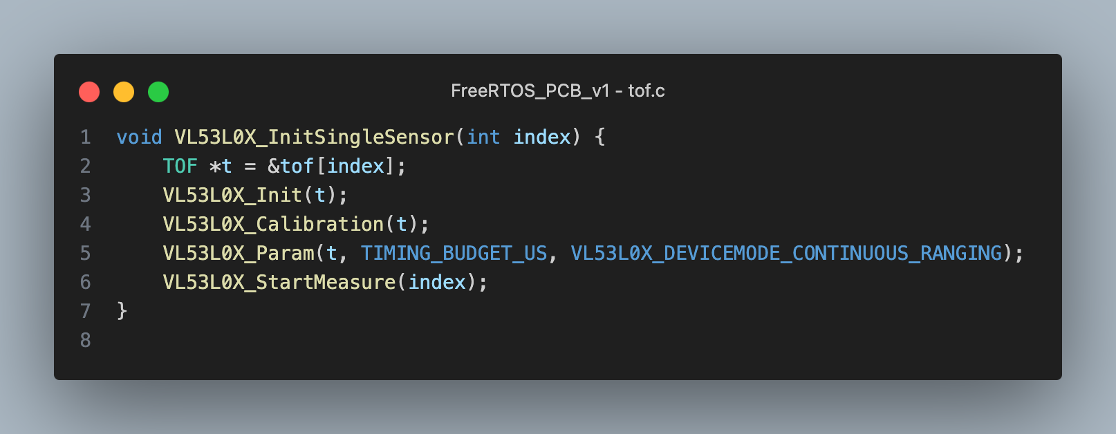
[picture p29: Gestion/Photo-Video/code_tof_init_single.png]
    
    <figcaption>Fonction d'initialisation d'un TOF</figcaption>
  </figure>
</figure>
<figure style="display:flex; gap:16px;">
  <figure style="text-align:center">
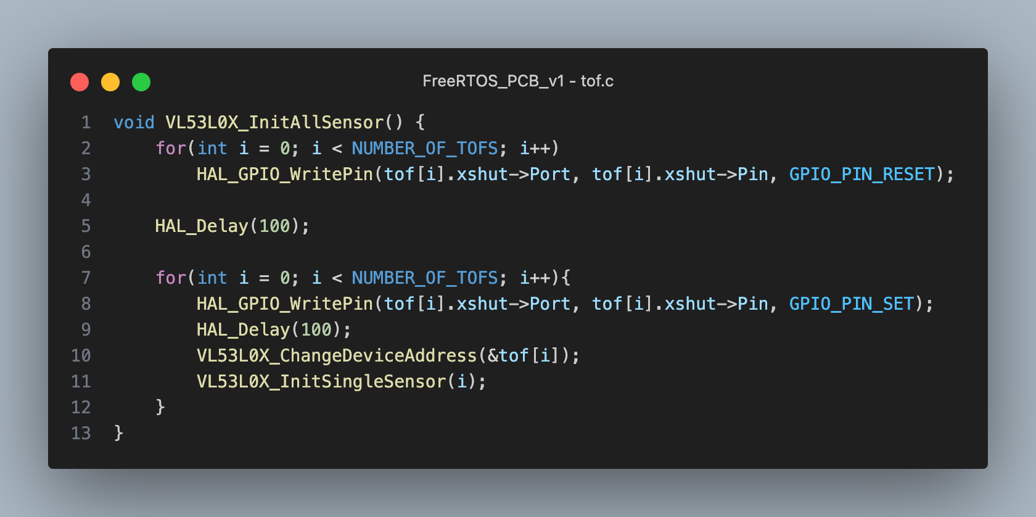
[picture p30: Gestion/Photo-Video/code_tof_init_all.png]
    
    <figcaption>Fonction d'initialisation de tous les TOFs</figcaption>
  </figure>
</figure>

L'ojectif des TOFs est uniquement de savoir si la distance perçue par le TOF est supérieure à une certaine distance seuil ou non. Dans le cas où la distance est supérieure à ce seuil alors le TOF "voit" le vide (en partant du principe que le robot est sur une table ou autre comme prévu dans l'énoncé du projet). 

<figure style="display:flex; gap:16px;">
  <figure style="text-align:center">
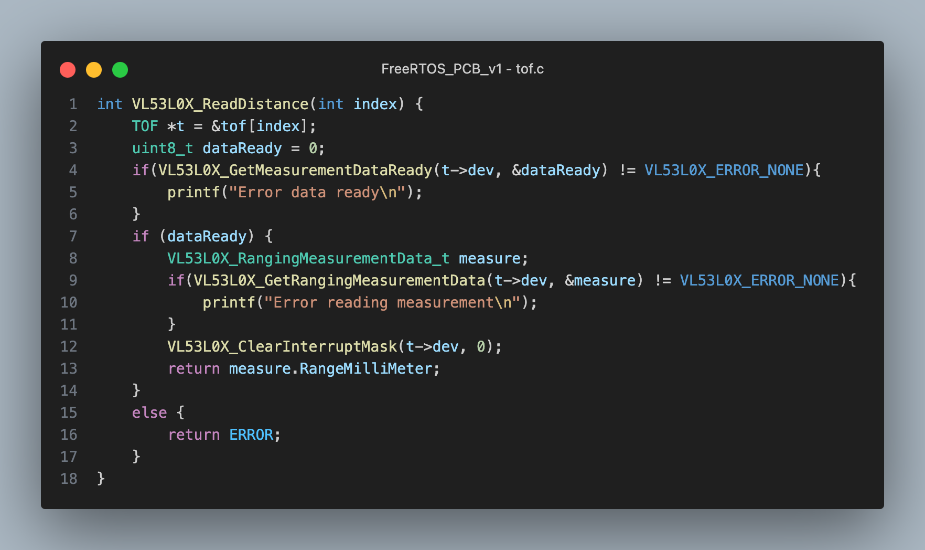
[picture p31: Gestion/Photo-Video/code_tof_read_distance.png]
    
    <figcaption>Fonction de lecture de la distance en mm</figcaption>
  </figure>
  <figure style="text-align:center">
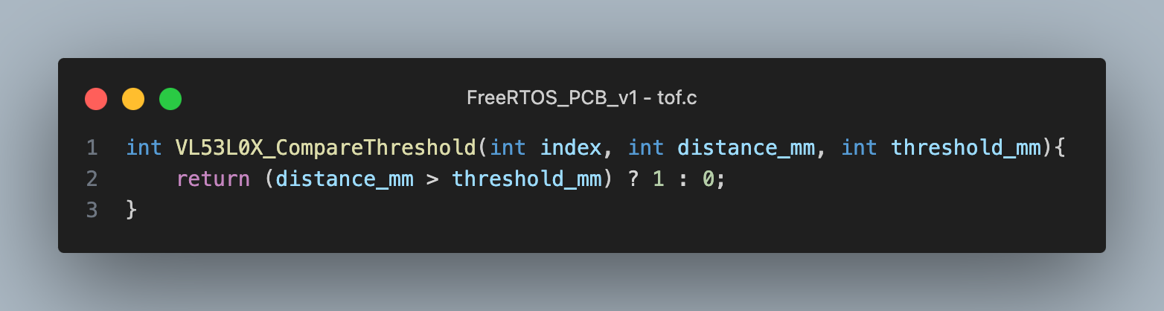
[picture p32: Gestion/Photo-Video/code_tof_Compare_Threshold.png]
    
    <figcaption>Fonction de comparaison au seuil</figcaption>
  </figure>
</figure>

<figure style="display:flex; gap:16px;">
  <figure style="text-align:center">
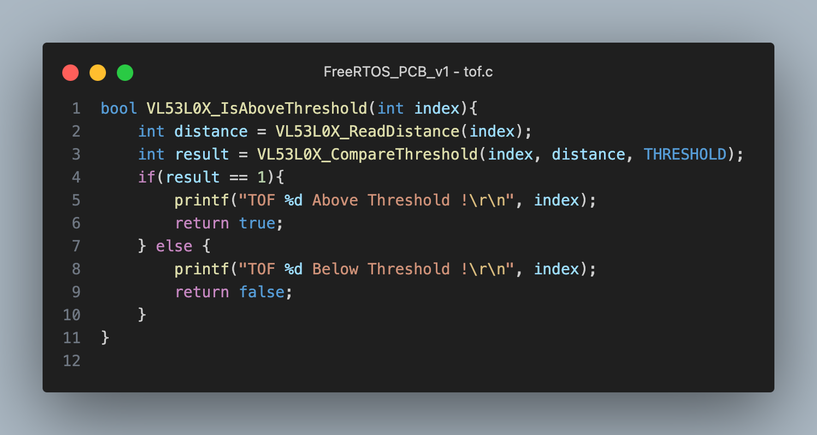
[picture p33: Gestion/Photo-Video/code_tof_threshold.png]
    
    <figcaption>Fonction de détection de seuil</figcaption>
  </figure>
</figure>

Dans le code principal il s'agit donc de vérifier un à un chacun des TOFs pour savoir si l'un d'entre eux perçoit une distance qui dépasse le seuil et si c'est le cas alors une mesure d'évitement est activée.

<figure style="display:flex; gap:16px;">
  <figure style="text-align:center">
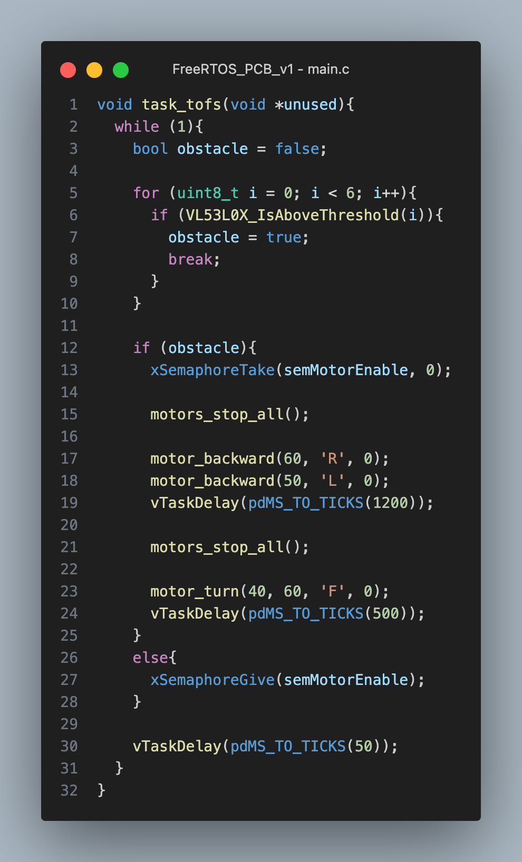
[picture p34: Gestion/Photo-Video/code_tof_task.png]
    
    <figcaption>Tâche FreeRTOS des TOFs</figcaption>
  </figure>
</figure>

### Accéléromètre

L'accéléromètre que nous utilisons ici est l'ADXL343, il est l'élément du robot qui va nous permettre de mettre à jour le rôle du robot, souris ou chat, dès lors qu'il y a un contact avec le robot adverse.

Une version de test de ce composant existe dans le dossier acc_test mais nous n'avons pas eu le temps d'implémenter cette partie dans le projet global (dossier FreeRTOS_PCB_v1). De plus, les conclusions des tests n'ont pas été partagées entre les membres de l'équipe donc nous ne pouvons pas affirmer si le code présent dans acc_test est correct ou non. 

D'un point de vue global, l'accéléromètre travaille sur les trois axes X,Y et Z et peut renvoyer les valeurs d'accélérations sur un ou plusieurs de ces axes en fonctions de la configuration des registres. Afin de détecter un contact avec le robot adverse on peut utiliser des registres permettant de répérer un Single-Tap ou un Double-Tap, cependant la question de la sensibilité du tap peut se poser. Une autre façon serait de comparer directement dans une fonction l'accélération reçue sur un ou plusieurs axes et la ou les comparées à un ou plusieurs seuils.

### LEDs

Comme expliqué rapidement dans la partie Hardware, nous utilisons pour ce projet un bandeau de LED Neopixel permettant d'indiquer selon quelles directions sont repérées les différents objets et parmi eu le robot adversaire via une LED d'une couleur différente des autres.
Pour réaliser cela nous avons repris une librairie créée par notre professeur afin d'envoyer un signal PWM via DMA au LEDs. Pour satisfaire notre application exacte nous avons créés différentes fonctions, dont une permettant d'allumer une LED en fonction de l'angle selon lequel le LiDAR a vu l'objet.

<figure style="display:flex; gap:16px;">
  <figure style="text-align:center">
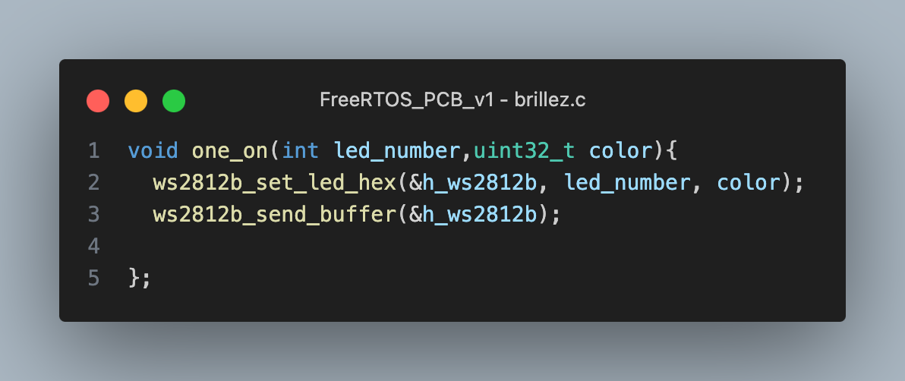
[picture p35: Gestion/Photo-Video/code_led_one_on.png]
    
    <figcaption>Fonction pour éteindre toutes les LEDs</figcaption>
  </figure>
  <figure style="text-align:center">
    
    <figcaption>Fonction pour allumer une LED</figcaption>
  </figure>
  <figure style="text-align:center">
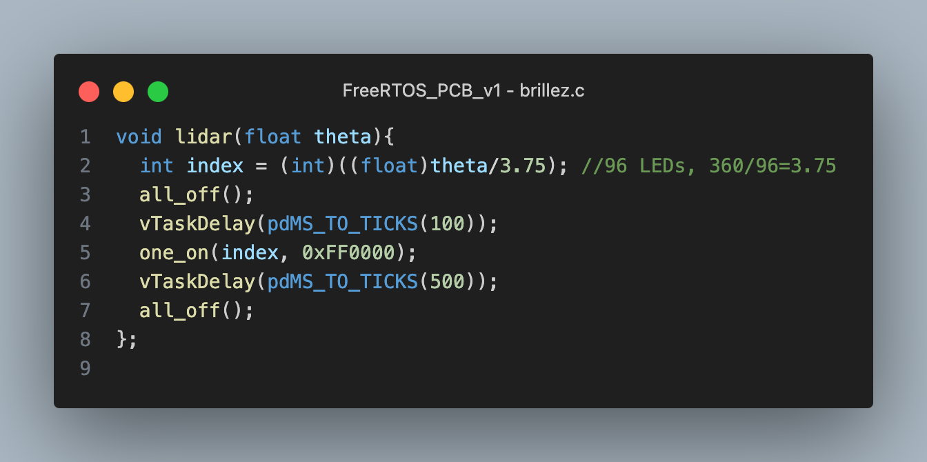
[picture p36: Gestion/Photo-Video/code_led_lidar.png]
    
    <figcaption>Fonction liée au LiDAR</figcaption>
  </figure>
</figure>

### Audio

Pour cette partie nous utilisons un driver créé dans un projet précédent pour communiquer en UART avec le module MP3 suivant : 38586 (GoTronic). Ce module contient directement un port pour y insérer une carte SD avec les sons que l'on veut jouer.

Malheuresement, nous n'avons pas eu le temps de travailler sur la liaison I2C avec le PCB dédié à l'amplificateur audio et donc nous n'avons pas pu entendre le son directement sur le haut-parleur bien qu'il soit écoutable directement avec un casque branché en mini-jack sur le module MP3.

### Raspberry Pi zero 2W

Cette partie n'ayant pas pu être traitée dans le temps impartis nous allons simplement revenir sur les aspects que la Raspberry Pi Zero 2W aurait dû ajouter au projet. 

Dans un premier temps, la Pi aurait du permettre d'afficher les données essentielles liées au robot par l'intermédiaire d'une liaison UART cadencée à 1 Mo de baud rate. Pour afficher ces données, il était prévu d'héberger sur la Pi un serveur Nginx afin de pouvoir, par cet intermédiaire, accéder à une interface graphique indiquant l'ensemble des données reçues ainsi que la "vision" du robot via un module camera Raspberry Pi connecté à la Pi zero 2W. 

De plus, l'ajout de cette Pi aurait dû permettre un contrôle du robot selon deux autres modes en plus de celui demandé initialement. En effet, le premier mode aurait été un contrôle à la manette type controller pro de Switch connécté en Bluetooth à la Pi et grâce à l'API gamepad en JS nous aurions pu détecter l'appui sur l'un des boutons et ainsi transmettre l'information au MCU via la liaison UART pour indiquer au robot les mouvements a effectuer. Le deuxème mode qui était prévu était un mode permettant de contrôler le robot par la voix grâce à une API Google de reconnaissance vocale dédiée.

# Résultat Final

Le résultat final a été présenté le Vendredi 16 Janvier après-midi devant les professeurs et le reste de la promotion. Pour cette démonstration finale nous avons pu montrer que le robot avance jusqu'à rencontrer un bord de table où il va reculer puis tourner vers la droite et répéter cette procédure indéfiniment. 

<figure style="display:flex; gap:16px;">
  <figure style="text-align:center">
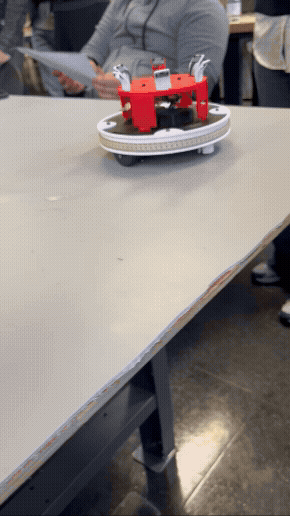
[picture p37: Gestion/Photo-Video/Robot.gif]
    
  </figure>
</figure>

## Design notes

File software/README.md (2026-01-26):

# Compte rendu partie software 

Ce compte rendu explique tous les codes du répertoire et rapporte ainsi des précisions sur les programmes du projet. 

## acc_test

Ce répertoire contient un projet STM32 avec pour cible le MCU STM32G431. 
Comme l'accéléromètre de notre carte ne fonctionnait pas, on a d'abord fait un programme qu'on a testé sur une ancienne carte.
Mais comme le driver est relativement bien écrit, je pense qu'il est facilement portable sur une autre cible STM.

Ce projet contient un programme qui configure l'accéléromètre ADXL350 en interruption sur SINGLE TAP, et permet ainsi de détecter les collisions avec les autres robots, pour ensuite changer de rôle chat-souris.

#### Configuration de l'accéleromètre 



#### Traitement de l'interruption 

La fonction `void ADXL343_IntCallback(h_ADXL343_t *h_ADXL343, uint16_t GPIO_Pin)` est a appelé dans la fonction de callback d'interruption `void HAL_GPIO_EXTI_Callback(uint16_t GPIO_Pin)`.
Dans cette fonction, une lecture dans le registre **`INT_SOURCE`** est nécessaire pour clear le flag d'interruption et ainsi permettre la réception de la prochaine interruption. 

## ancien_pcb

## lidar_nucleo

Ce répertoire contient un code permettant de réceptionner et traiter les données lidar et détecter la cible qui est la lidar d'un autre robot.



#### Reception et traitement de données lidar 

- Le LiDAR communique avec le microcontrôleur via une liaison UART.
La réception des données repose sur l’utilisation de l’interruption IDLE, déclenchée lorsque la ligne RX reste inactive pendant un certaine durée signifiant la fin d'une trame.
Cette interruption est exploitée pour détecter la fin d’une trame de données et initier le traitement des informations reçues.

- Le traitement des données est fait en suivant le [manuel du protocole](https://github.com/YDLIDAR/YDLidar-SDK/blob/master/doc/YDLidar-SDK-Communication-Protocol.md) du constructeur. 
Après la réception d’une trame complète, celle-ci est d’abord validée en vérifiant la présence du header ainsi que l’intégrité des données à l’aide du checksum.
Une fois la trame jugée valide, les champs principaux sont extraits, notamment le nombre d’échantillons (LSN), l’angle de départ de mesure (FSA) et l’angle de fin de mesure (LSA).
Ces informations permettent ensuite de calculer la correspondance entre chaque échantillon de distance et son angle de mesure associé.

#### Algo de détection de cible

- L’algorithme de détection de cible repose sur la connaissance a priori des dimensions de la cible, constituée d’un cylindre de 6 cm de diamètre, correspondant à un second LiDAR.
- Les données de distance, stockées sous forme circulaire, sont parcourues afin d’analyser l’environnement sur 360°.
- Pour chaque mesure de distance, l’ouverture angulaire théorique correspondant à un cylindre de 6 cm est calculée en fonction de la distance mesurée.
- Cette ouverture angulaire permet d’identifier des ensembles d’échantillons contigus susceptibles de correspondre à une cible réelle.
Une liste de cibles potentielles est alors extraite, parmi laquelle seule la cible la plus proche est conservée, les objets éloignés présentant une probabilité plus élevée de faux positifs.

## tof_g747

Ce programme TOF n'est pas celui utilisé dans le code rassemblé pour la démonstration, mais je trouve qu'il est bien parce que les tof sont configuré pour envoyé une interruption sur dépassement de seuil, on n'a donc pas à faire la comparaison de la distance à chaque réception d'interruption.

#### Configuation des capteurs TOF



- Les capteurs TOF VL53L0X fonctionne avec une communication I2C dont les registres ne sont pas ouvertement indiqué dans la datasheet qui nous recommande d'utiliser le driver fourni par le constructeur.
- Comme nous prévoyons 6 capteurs sur un même bus I2C et que l'addresse device par défaut des TOFs est toujours la même, nous utilisons le pin XSHUT du capteur pour activer puis configurer sans oublier de changer l'addresse device des TOF un à un, pour ensuite pouvoir manipuler les 6 TOFs correctement.
- Les étapes de configuation suivent les étapes indiqués dans le [manuel de référence](https://www.st.com/resource/en/user_manual/um2039-world-smallest-timeofflight-ranging-and-gesture-detection-sensor-application-programming-interface-stmicroelectroni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)

#### Traitement des interruptions

- Le pin d'interruption GPIO détectant un front montant correspond au tof dont le dépassement de seuil est détecté, on utilise `VL53L0X_ClearInterruptMask(tof_devices[i].dev, VL53L0X_GPIOFUNCTIONALITY_THRESHOLD_CROSSED_HIGH);` pour clear le flag d'interrupion du côté du TOF pour que celui-ci puisse envoyer les prochaines interruptions.

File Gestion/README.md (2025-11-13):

# Projet ESE – Chat Robot  
**Point à mi-parcours – 13 novembre 2025**

Je propose ici de faire un point sur l’ensemble du projet tel qu’il a été défini à la date d’aujourd’hui.

---

## Partie hardware

Commençons par la partie hardware du projet, en détaillant l’ensemble des périphériques présents sur le PCB :

### TOFs  
Le robot est équipé de six capteurs TOF, disposés en cercle et orientés en biais (environ 45° selon la conception actuelle). Cette disposition permet d’obtenir une “vision” plus étendue (environ une dizaine de centimètres) de l’environnement autour du robot, plutôt que de se limiter à une détection verticale à la base.

### Module MP3  
Le connecteur est relié à un module MP3 communiquant en UART. Ce module permet d’insérer une carte microSD contenant des fichiers audio. Via l’UART, il est possible de sélectionner le fichier à lire et de régler le volume de sortie.  
La sortie audio (mini-jack) est connectée à un PCB annexe — actuellement en commande — qui amplifie le signal avant de l’envoyer à un haut-parleur.  
Ce système sera utilisé lors de moments clés de la démonstration, notamment lorsque le robot changera de rôle après une collision, afin d’indiquer s’il est “devenu” un chat ou une souris.

### LEDs  
Nous utilisons un ruban de LEDs Neopixel qui viendra en soutien au LiDAR pour indiquer la direction dans laquelle le robot adverse a été détecté.  
Elles serviront également, à l’instar du haut-parleur, à signaler les changements de rôle du robot.

### Raspberry Pi Zero 2W  
Un Raspberry Pi Zero 2W est ajouté au PCB afin d’héberger une interface graphique utilisateur (GUI) accessible en ligne.  
Cette interface permettra d’obtenir une “vision” du robot grâce à une caméra embarquée, ainsi que de visualiser diverses constantes et mesures telles que la vitesse, l’accélération ou encore le niveau de batterie du robot.

---

## Partie software

Concernant la partie **logicielle**, voici l’état d’avancement et l’organisation du travail à ce jour :

### Drivers développés
À l’heure actuelle, plusieurs drivers ont déjà été créés pour les périphériques mentionnés ci-dessus :

- **LEDs** : fonctionnel  
- **MP3** : fonctionnel  
- **TOFs** : améliorable  
- **Moteurs** : en cours de développement  
- **LiDAR** : en cours de développement  

La prochaine étape consistera à finaliser ces drivers, puis à travailler sur l’aspect noyau temps réel du projet à l’aide de FreeRTOS.  
Ce dernier nous permettra de faire fonctionner simultanément l’ensemble des modules pour aboutir à un robot pleinement opérationnel.

### Évolutions envisagées
Dans la perspective d’un système complet, plusieurs idées ont émergé, notamment :  
- la connexion d’une manette Bluetooth (type console) à la Raspberry Pi pour piloter le robot ;  
- l’intégration de commandes vocales pour une interaction plus naturelle.

---

## Partie mécanique

Enfin, la modélisation 3D du robot est pratiquement terminée.  
Quelques ajustements mineurs restent à effectuer, notamment au niveau de la base.  
Le principal point de réflexion concerne les roues, qui ont été modifiées pour être élargies par l’ajout d’un second joint torique sur chacune d’elles.  
Cependant, cette modification pourrait compliquer le contrôle du robot, car elle transforme le point de contact unique en aire de contact, ce qui pourrait affecter la maniabilité.

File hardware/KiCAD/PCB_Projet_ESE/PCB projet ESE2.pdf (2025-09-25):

'Reference' | 'Qty' | 'Value' | 'Footprint'
'BUxxSD1' | '1' | '~' | 'RÃ©gu:SSOP5_BUxxSD5'
'C1,C2,C8,C10,C11,C12,C13,C14,C17,C19,C21,C22,C23,C29' | '14' | '100n' | 'Capacitor_SMD:C_0402_1005Metric'
'C3,C4,C6' | '3' | '4u7' | 'Capacitor_SMD:C_0603_1608Metric'
'C9,C16,C18,C27,C28' | '5' | '1u' | 'Capacitor_SMD:C_0603_1608Metric'
'C15' | '1' | '10n' | 'Capacitor_SMD:C_0402_1005Metric'
'C20' | '1' | '22u' | 'Capacitor_SMD:C_1206_3216Metric'
'C24' | '1' | '15p' | 'Capacitor_SMD:C_0402_1005Metric'
'C25,C26' | '2' | '22u' | 'Capacitor_SMD:C_0603_1608Metric'
'C30' | '1' | '10u' | 'Capacitor_SMD:C_0603_1608Metric'
'D2,D3,D4' | '3' | 'LED' | 'LED_SMD:LED_0603_1608Metric'
'D5' | '1' | 'D_TVS_Small' | 'Diode_SMD:D_SOD-523'
'F2' | '1' | '3.3A' | 'Fuse:Fuse_2920_7451Metric'
'H1,H2,H3,H4' | '4' | 'MountingHole_Pad' | 'MountingHole:MountingHole_3.2mm_M3_Pad_Via'
'J1,J3' | '2' | 'Conn_01x06' | 'Connector_JST:JST_PH_S6B-PH-K_1x06_P2.00mm_Horizontal'
'J2' | '1' | 'Conn_01x04' | 'Connector_JST:JST_SH_BM04B-SRSS-TB_1x04-1MP_P1.00mm_Vertical'
'J4' | '1' | 'Conn_01x03' | 'Connector_JST:JST_PH_B3B-PH-K_1x03_P2.00mm_Vertical'
'J7,J16' | '2' | 'Conn_01x04' | 'Connector_JST:JST_PH_B4B-PH-K_1x04_P2.00mm_Vertical'
'J8' | '1' | 'Conn_01x02' | 'Connector_AMASS:AMASS_XT30U-M_1x02_P5.0mm_Vertical'
'J9' | '1' | 'Conn_ST_STDC14' | 'Connector_PinHeader_1.27mm:PinHeader_2x07_P1.27mm_Vertical_SMD'
'J10,J11,J12,J13,J14,J15' | '6' | 'Conn_01x06' | 'Connector_JST:JST_SH_BM06B-SRSS-TB_1x06-1MP_P1.00mm_Vertical'
'L1' | '1' | '39n' | 'Inductor_SMD:L_0603_1608Metric'
'L2' | '1' | '4u7' | 'Inductor_SMD:L_0603_1608Metric'
'MP1' | '1' | '~' | 'RÃ©gu:TSOT23-8'
'R1,R4,R8,R9' | '4' | '1k' | 'Resistor_SMD:R_0402_1005Metric'
'R2' | '1' | '20k' | 'Resistor_SMD:R_0402_1005Metric'
'R3' | '1' | '5k6' | 'Resistor_SMD:R_0402_1005Metric'
'R5' | '1' | '2k9' | 'Resistor_SMD:R_0402_1005Metric'
'R6' | '1' | '1k65' | 'Resistor_SMD:R_0402_1005Metric'
'R7' | '1' | '800' | 'Resistor_SMD:R_0402_1005Metric'
'R10,R11' | '2' | '100k' | 'Resistor_SMD:R_0402_1005Metric'
'R12' | '1' | '20' | 'Resistor_SMD:R_0402_1005Metric'
'R13' | '1' | '16k' | 'Resistor_SMD:R_0402_1005Metric'
'R14' | '1' | '7k68' | 'Resistor_SMD:R_0402_1005Metric'
'R15' | '1' | '40k2' | 'Resistor_SMD:R_0402_1005Metric'
'SW1' | '1' | 'SW_SPST' | 'RÃ©gu:SW_SPST'
'SW2' | '1' | '472121010111' | 'RÃ©gu:SW_Wurth_WS-TOTV_472123020421'
'TP1,TP2,TP3,TP4,TP5,TP6' | '6' | 'TestPoint' | 'TestPoint:TestPoint_Pad_D1.0mm'
'U1,U2' | '2' | 'ZXBM5210-SP' | 'Package_SO:Diodes_SO-8EP'
'U3' | '1' | 'STM32G474RETx' | 'Package_QFP:LQFP-64_10x10mm_P0.5mm'
'U4' | '1' | 'ADXL343' | 'Package_LGA:LGA-14_3x5mm_P0.8mm_LayoutBorder1x6y'

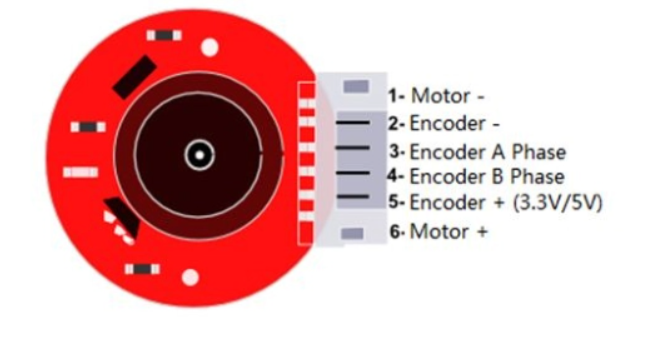
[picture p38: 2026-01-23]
Gestion/Photo-Video/fit0520pinout.png

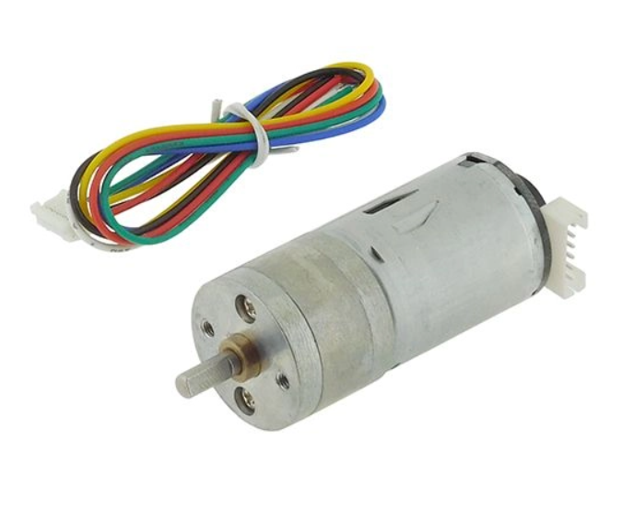
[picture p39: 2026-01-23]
Gestion/Photo-Video/fit0520.png

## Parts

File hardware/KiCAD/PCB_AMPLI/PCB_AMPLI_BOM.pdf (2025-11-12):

PCB_AMPLI

Reference | Qty Value
C1,C2,C3,C7 | 4 100n
C4 | 1 1u
C5 | 1 2u2
C6 | 1 10u
D1 | 1 GREEN_LED
D2 | 1 RED_LED
D3 | 1 BLUE_LED
H1,H2 | 2 MountingHole_Pad
J2 | 1 Conn_01x02
J3,J4,J10 | 3 Conn_01x04
R1 | 1 1k8
R2 | 1 1k
R3 | 1 | 510
R4,R5 | 2 5k
R6 | 1 1k5
SW1,SW2,SW3 3 SW_SPDT
U1 | 1 ~

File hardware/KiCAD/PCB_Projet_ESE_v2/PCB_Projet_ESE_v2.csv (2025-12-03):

Reference | Qty | Value | DNP | Exclude from BOM | Exclude from Board
BUxxSD1,D20,LM1,LM2,LM3,MP1,SW1,SW2,TP12,U7,U8,U9,U10,U11,U12,U13,U14,U15 | 18 | ~
C1,C2,C3,C4,C7,C8,C9,C10,C11,C12,C13,C15,C16,C17,C18,C21,C24,C25,C26,C27,C28,C32,C33,C35,C36,C37,C43,C44,C45,C46,C47,C48,C50,C51,C52,C53,C58,C59,C60,C61,C62,C63,C64,C65,C66,C67,C68,C69,C70,C71,C72 | 51 | 100n
C5,C6,C20,L2,L3 | 5 | 4u7
C14,C56,C57 | 3 | 10u
C19,C23,C38 | 3 | 15p
C22,C30,C31,C41,C42,C54,C55 | 7 | 1u
C29 | 1 | 10n
C34,C39,C40 | 3 | 22u
C49 | 1 | D8L6.5_865090349007
D1,D21,D22,D23,D24,D25 | 6 | BLUE_LED_0402
D2 | 1 | BLUE_LED
D3,D4,D5 | 3 | LED
D6,D9 | 2 | Green LED
D7,D8 | 2 | YELLOW_LED
D10,D11 | 2 | Yellow LED
D12,D13 | 2 | Orange LED
D14,D15 | 2 | Amber LED
D16,D17 | 2 | Red LED
D18,D19 | 2 | Super Red LED
F1 | 1 | 1A
H1 | 1 | MountingHole_Pad
H2,H3,H4 | 3 | MountingHole_Pad |  | Exclure de la Liste du Matériel
J1,J2 | 2 | Conn_01x06
J4 | 1 | Conn_01x03
J5,J6 | 2 | Conn_01x04
J9 | 1 | Conn_01x02
J10 | 1 | Conn_ST_STDC14
L1 | 1 | 39n
R1,R2 | 2 | 3m
R3,R4,R5,R6 | 4 | 5k6
R7,R8,R21,R22,R73,R74 | 6 | 4k7
R9 | 1 | 56k
R10,R18 | 2 | 16k
R11 | 1 | 39
R12 | 1 | 2k7
R13,R33,R34 | 3 | 1k6
R14 | 1 | 820
R15,R16,R52,R54,R69,R71 | 6 | 100k
R17 | 1 | 20
R19 | 1 | 7k68
R20 | 1 | 40k2
R23,R24,R37,R38 | 4 | 1k
R25,R26,R27,R28,R39,R40 | 6 | 200
R29 | 1 | 48k7
R30 | 1 | 39k2
R31,R32 | 2 | 3k3
R35,R36 | 2 | 2k
R43,R44 | 2 | 1k3
R45,R46 | 2 | 2k4
R51,R72 | 2 | 5k23
R53,R70 | 2 | 11k
R55,R57,R59,R64,R66,R68 | 6 | 20k
R56,R67 | 2 | 78k7
R58 | 1 | 46k4
R60,R63 | 2 | 30k
R61,R62 | 2 | 47k
R65 | 1 | 46.4k
SW4,SW5 | 2 | SW_SPDT
TP1,TP2,TP3,TP4,TP5,TP6,TP7,TP8,TP9,TP10,TP11 | 11 | TestPoint
U1,U2 | 2 | ZXBM5210-SP
U3,U4 | 2 | NCS210
U5 | 1 | STM32G474RETx
U6 | 1 | ADXL343
U16 | 1 | MCP1802x-xx02xOT
Y1 | 1 | Crystal_GND24_Small

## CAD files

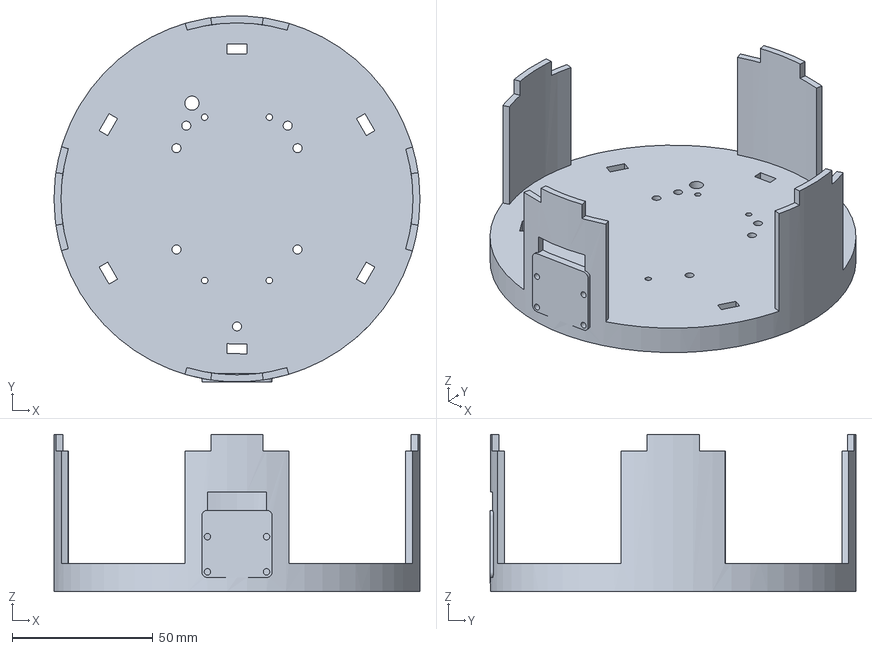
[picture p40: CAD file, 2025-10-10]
hardware/Onshape/anciennes_versions/v4/3mf/baseTOP.3mf
130.0 x 129.9 x 55.8 mm

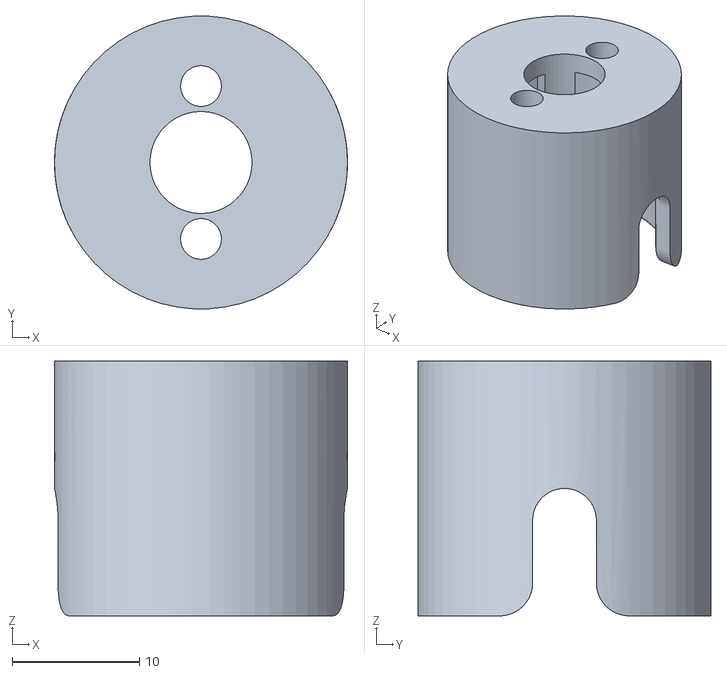
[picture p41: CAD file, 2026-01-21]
hardware/Onshape/Support_Bille.stl
23.0 x 23.0 x 20.0

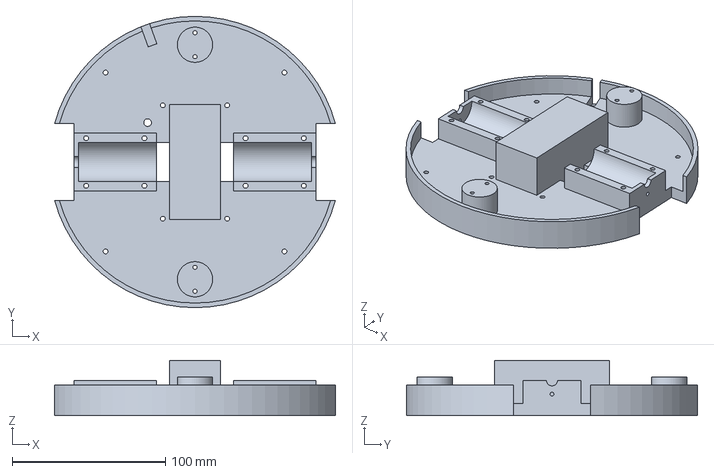
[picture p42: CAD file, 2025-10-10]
hardware/Onshape/anciennes_versions/v4/3mf/base.3mf
183.3 x 190.0 x 36.0 mm

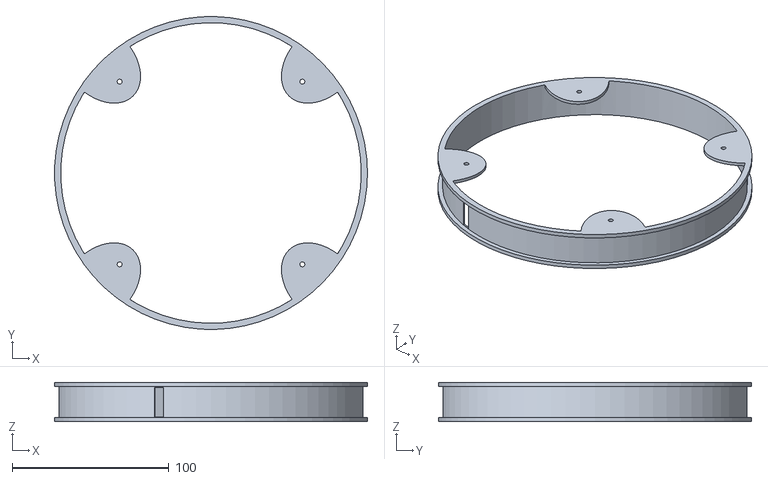
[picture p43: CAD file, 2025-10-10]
hardware/Onshape/anciennes_versions/v4/stl/Part3_v4.stl
200.0 x 200.0 x 25.0

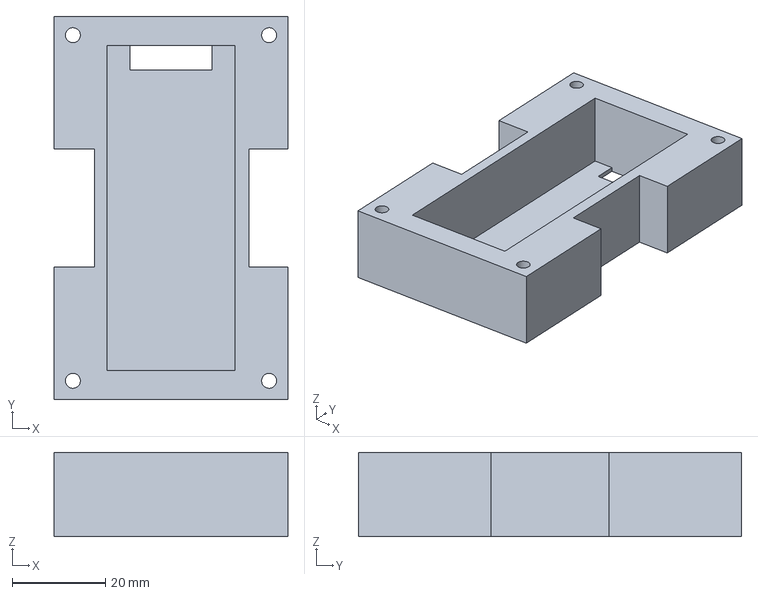
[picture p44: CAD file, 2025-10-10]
hardware/Onshape/anciennes_versions/v4/3mf/Li-ion_cache.3mf
50.0 x 82.0 x 18.0 mm

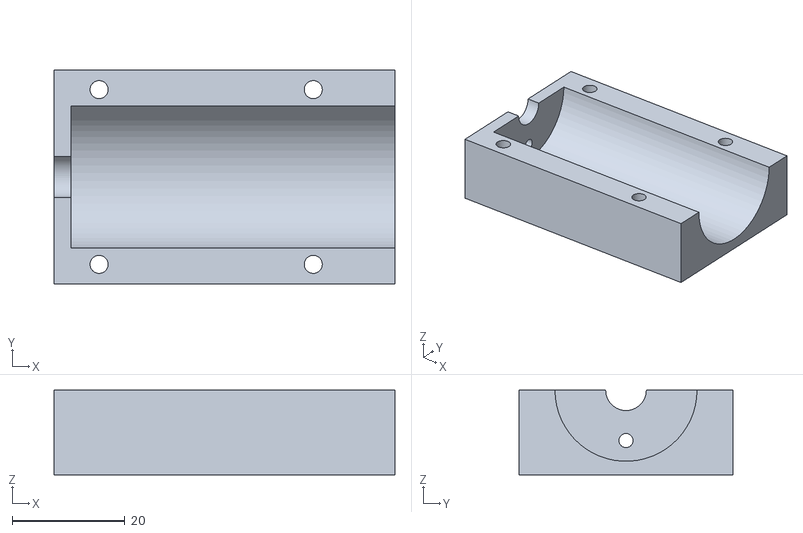
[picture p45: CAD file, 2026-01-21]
hardware/Onshape/Support_Moteur.stl
60.5 x 38.0 x 15.0

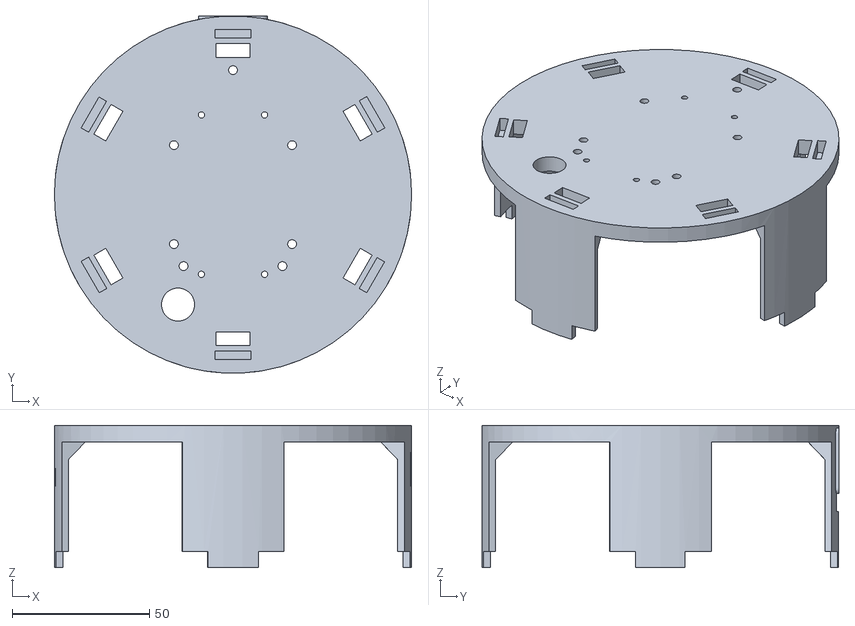
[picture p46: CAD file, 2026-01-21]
hardware/Onshape/Etage.stl
130.0 x 129.9 x 51.8

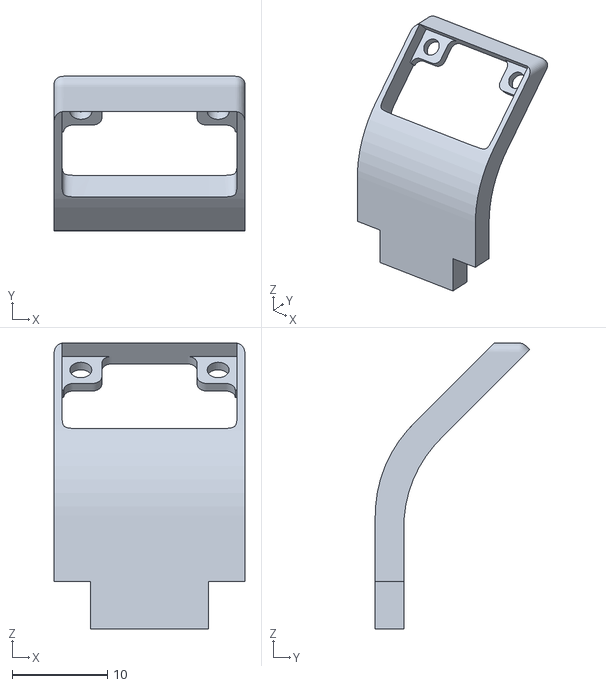
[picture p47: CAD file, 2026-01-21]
hardware/Onshape/Support_TOF.stl
20.0 x 16.2 x 30.0

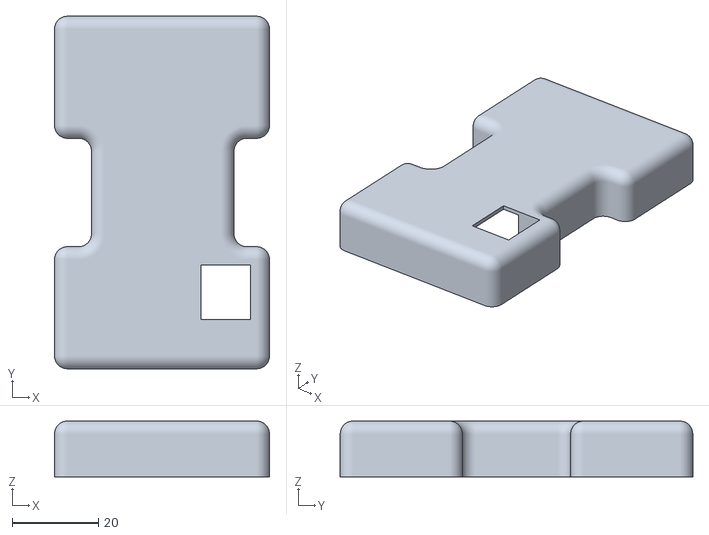
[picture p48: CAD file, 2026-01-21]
hardware/Onshape/Cache_Batterie.stl
50.0 x 82.0 x 13.0

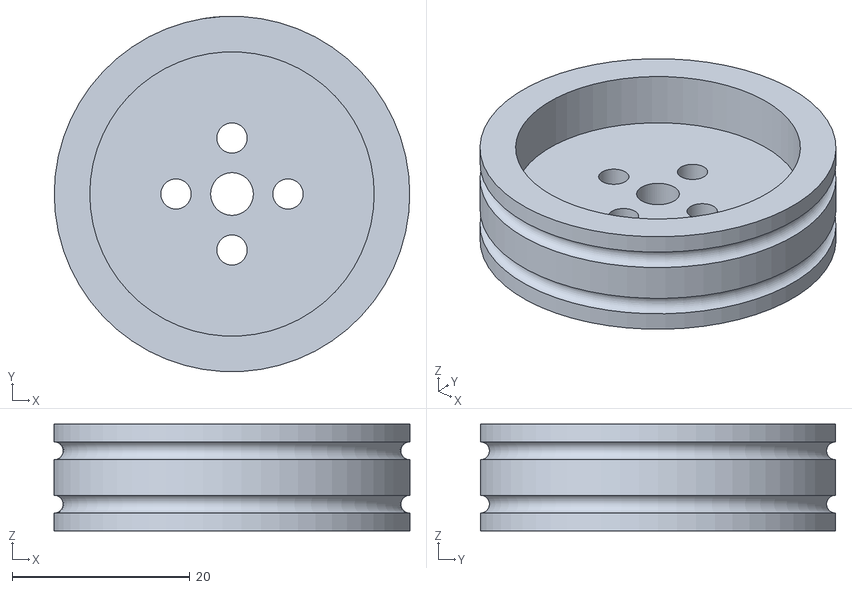
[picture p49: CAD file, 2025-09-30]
hardware/Onshape/Roue.stl
40.0 x 39.9 x 12.0

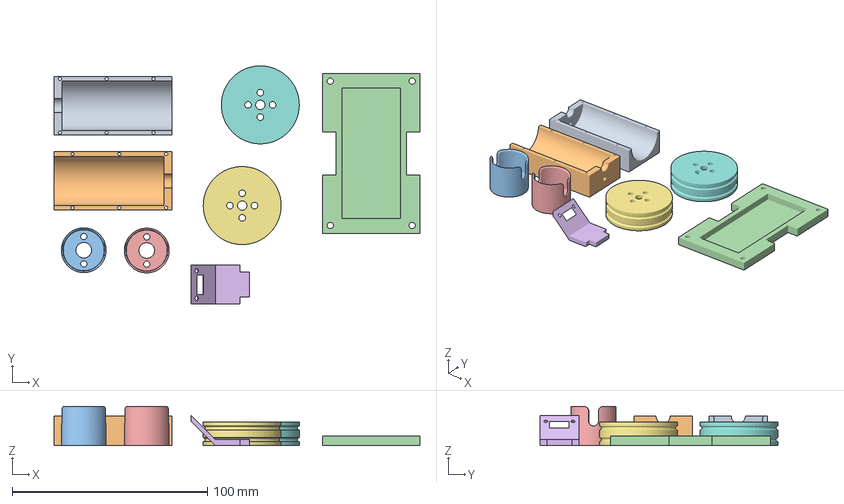
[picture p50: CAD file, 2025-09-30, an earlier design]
hardware/Onshape/anciennes_versions/v1/3mf/Part_2_3_4_5_6_9_R.3mf
187.7 x 122.1 x 20.0 mm
Part 2.stl
Part 3.stl
Part 4.stl
Part 5.stl
Part 6.stl
Part 9.stl
roue.stl x 2

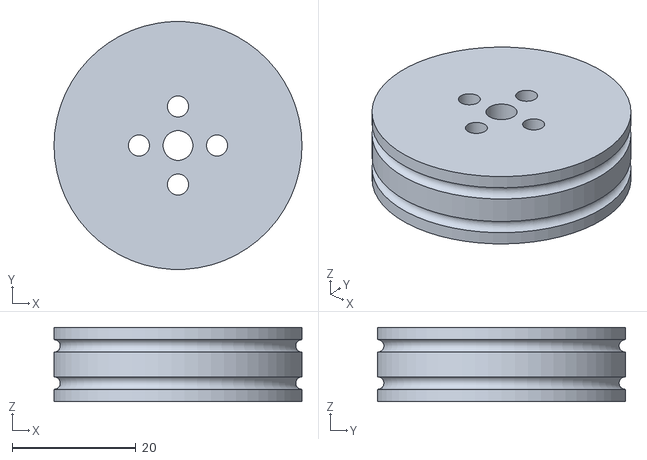
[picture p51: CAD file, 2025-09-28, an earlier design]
hardware/Onshape/anciennes_versions/v1/stl/roue.stl
40.0 x 39.9 x 12.0

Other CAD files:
hardware/Onshape/anciennes_versions/v4/stl/Part4_v4.stl
hardware/Onshape/Base.stl
hardware/Onshape/anciennes_versions/v4/stl/Part2_v4.stl
hardware/Onshape/anciennes_versions/v4/3mf/LED.3mf
hardware/Onshape/anciennes_versions/v4/stl/Part1_v4.stl
hardware/Onshape/anciennes_versions/v1/3mf/Part_1.3mf
hardware/Onshape/anciennes_versions/v1/3mf/Part_7.3mf
hardware/Onshape/anciennes_versions/v1/3mf/Part_8.3mf
hardware/Onshape/anciennes_versions/v1/stl/Part_1.stl
hardware/Onshape/anciennes_versions/v1/stl/Part_2.stl
hardware/Onshape/anciennes_versions/v1/stl/Part_3.stl
hardware/Onshape/anciennes_versions/v1/stl/Part_4.stl
hardware/Onshape/anciennes_versions/v1/stl/Part_5.stl
hardware/Onshape/anciennes_versions/v1/stl/Part_6.stl
hardware/Onshape/anciennes_versions/v1/stl/Part_7.stl
hardware/Onshape/anciennes_versions/v1/stl/Part_8.stl
hardware/Onshape/anciennes_versions/v1/stl/Part_9.stl
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

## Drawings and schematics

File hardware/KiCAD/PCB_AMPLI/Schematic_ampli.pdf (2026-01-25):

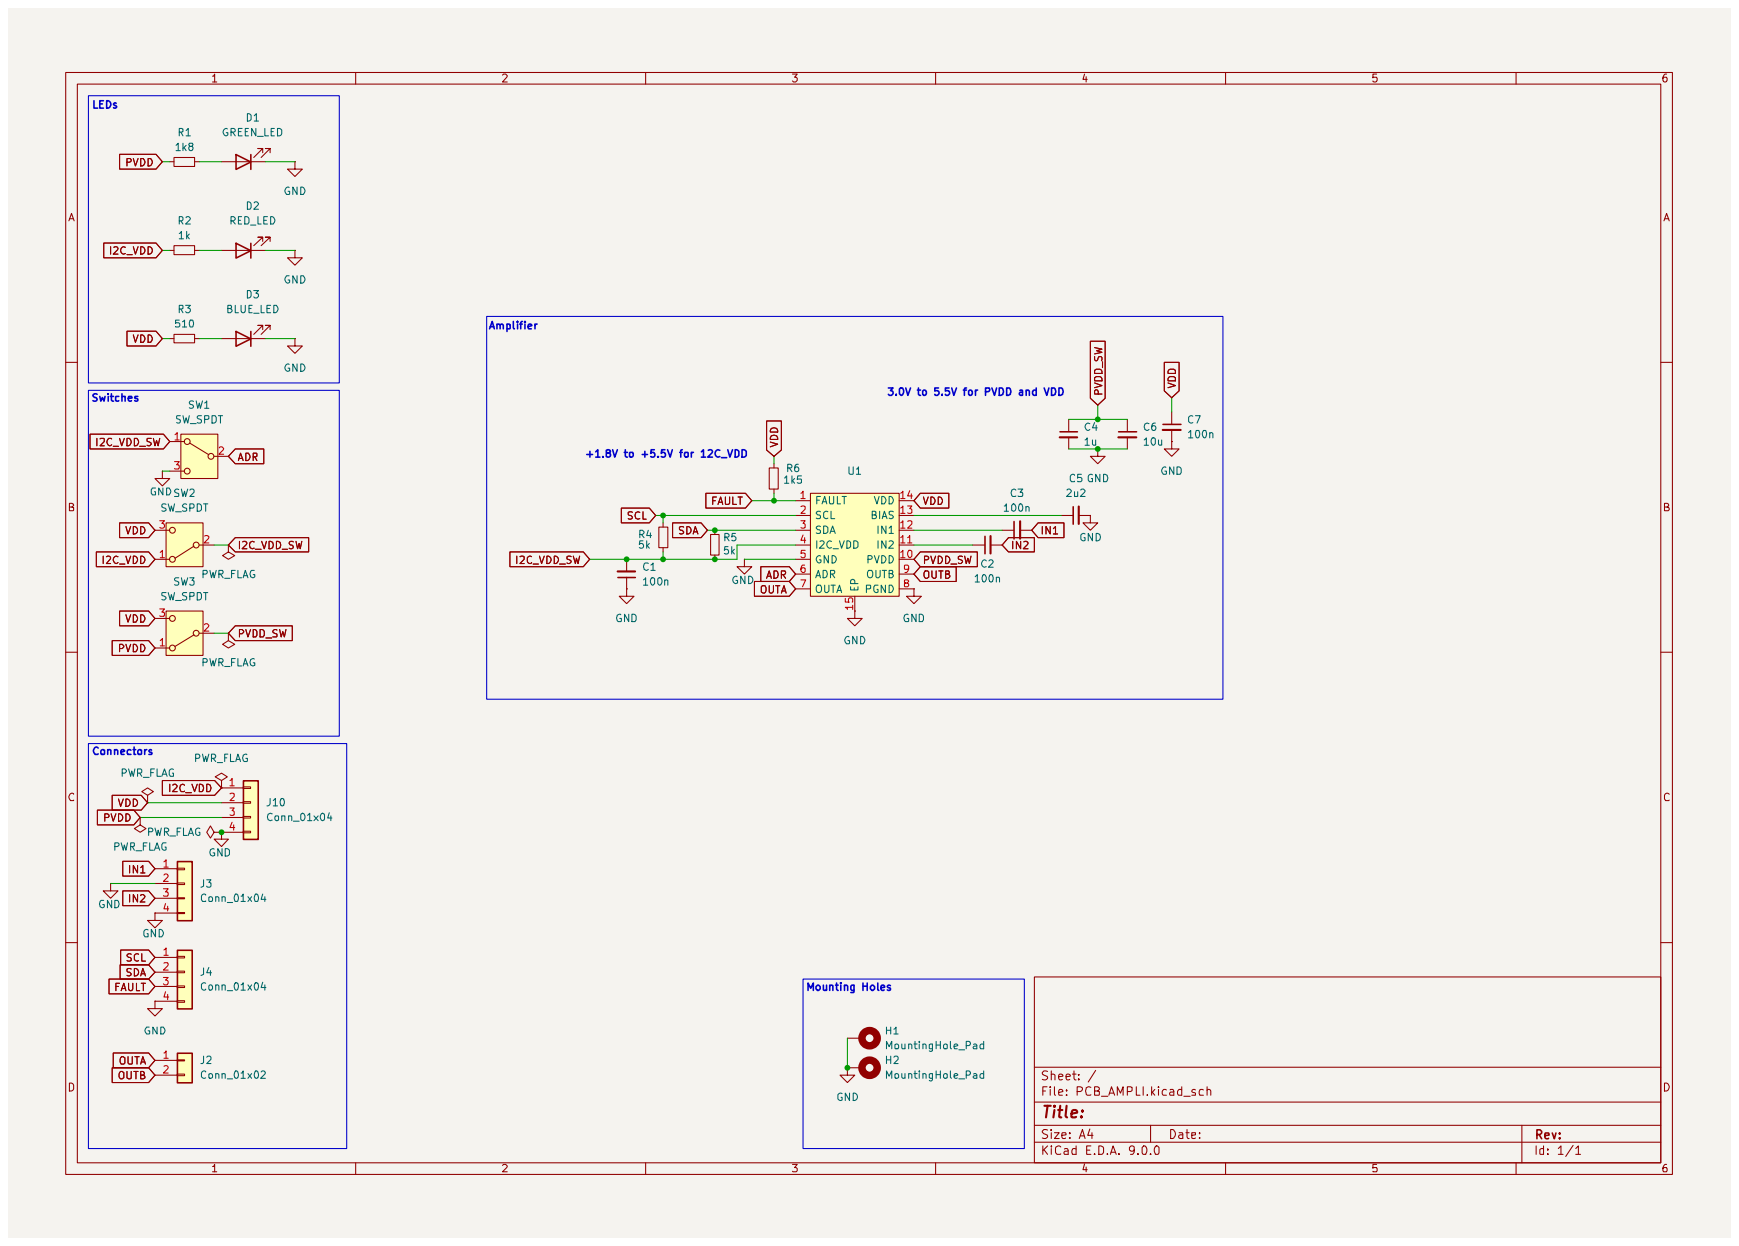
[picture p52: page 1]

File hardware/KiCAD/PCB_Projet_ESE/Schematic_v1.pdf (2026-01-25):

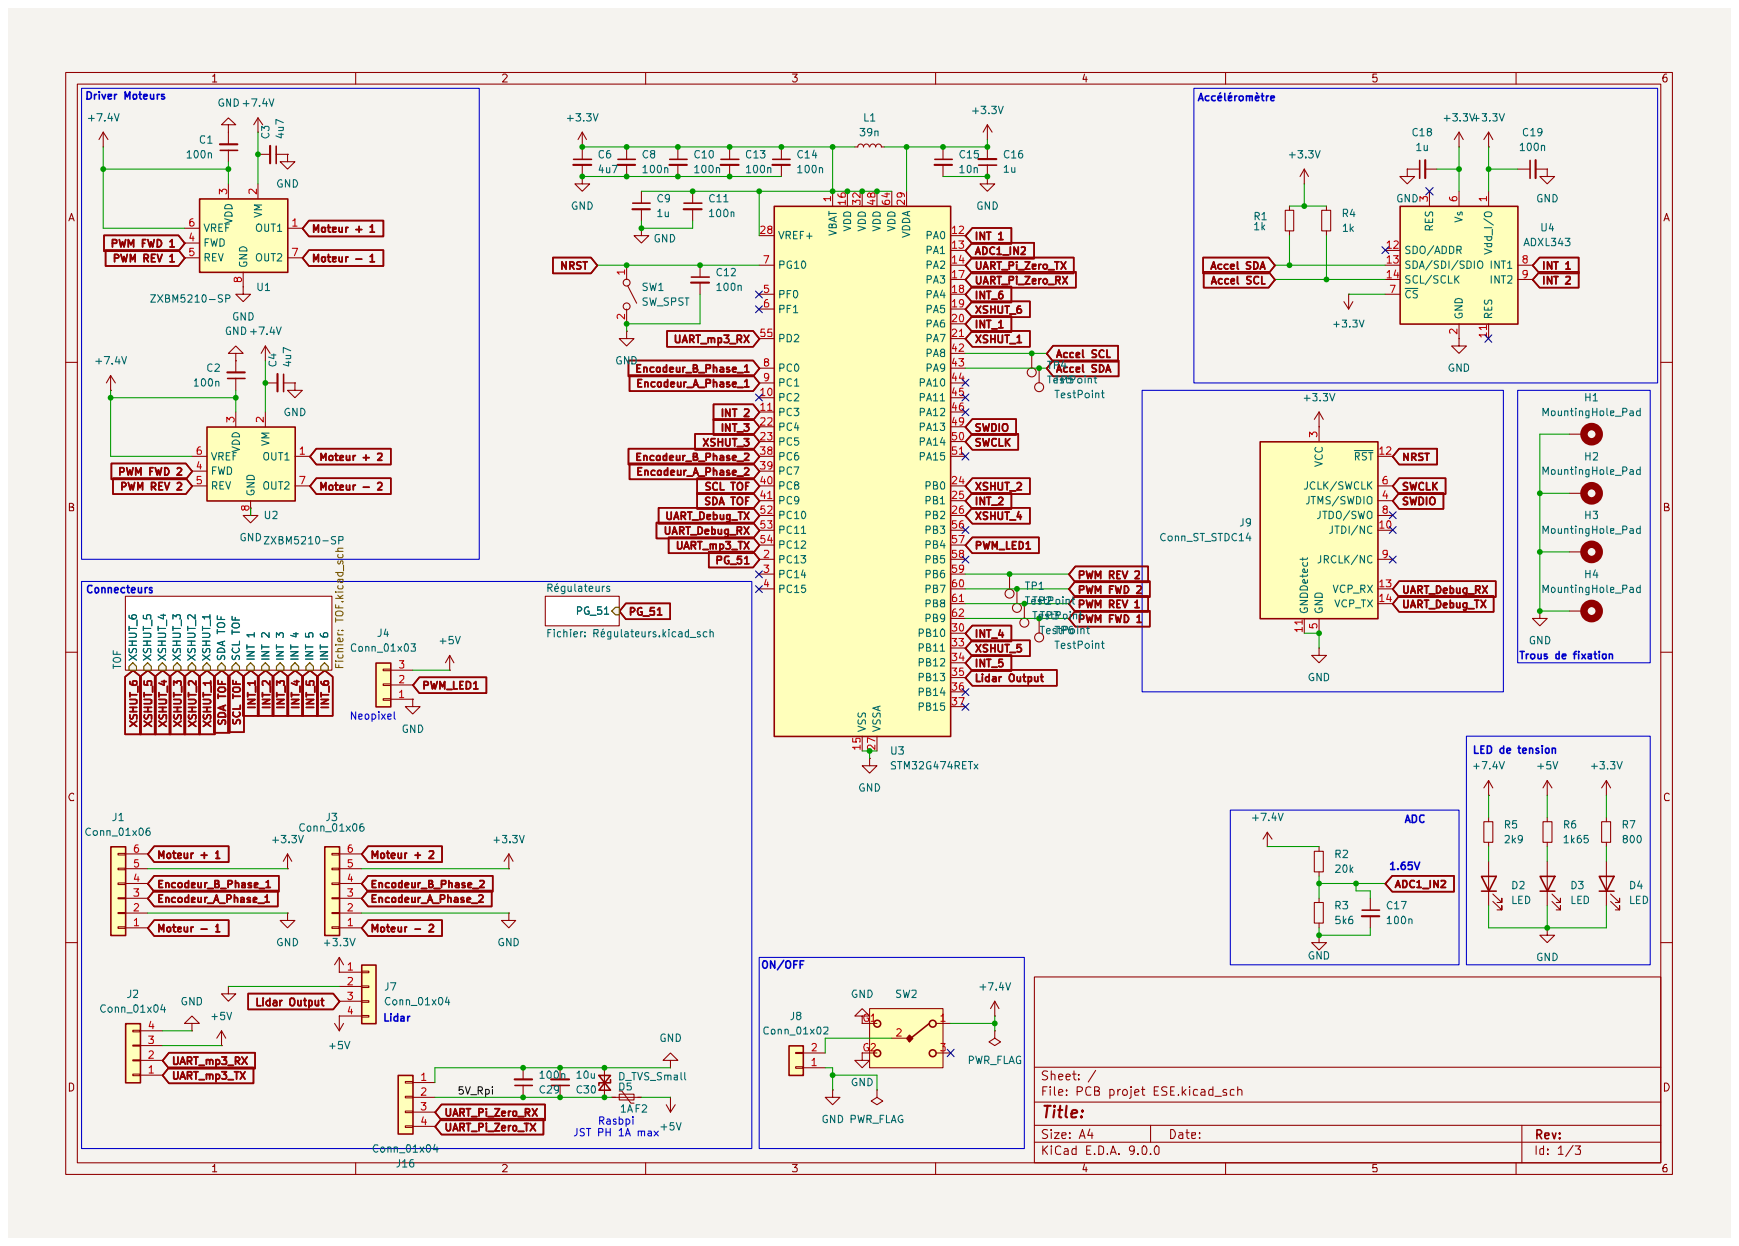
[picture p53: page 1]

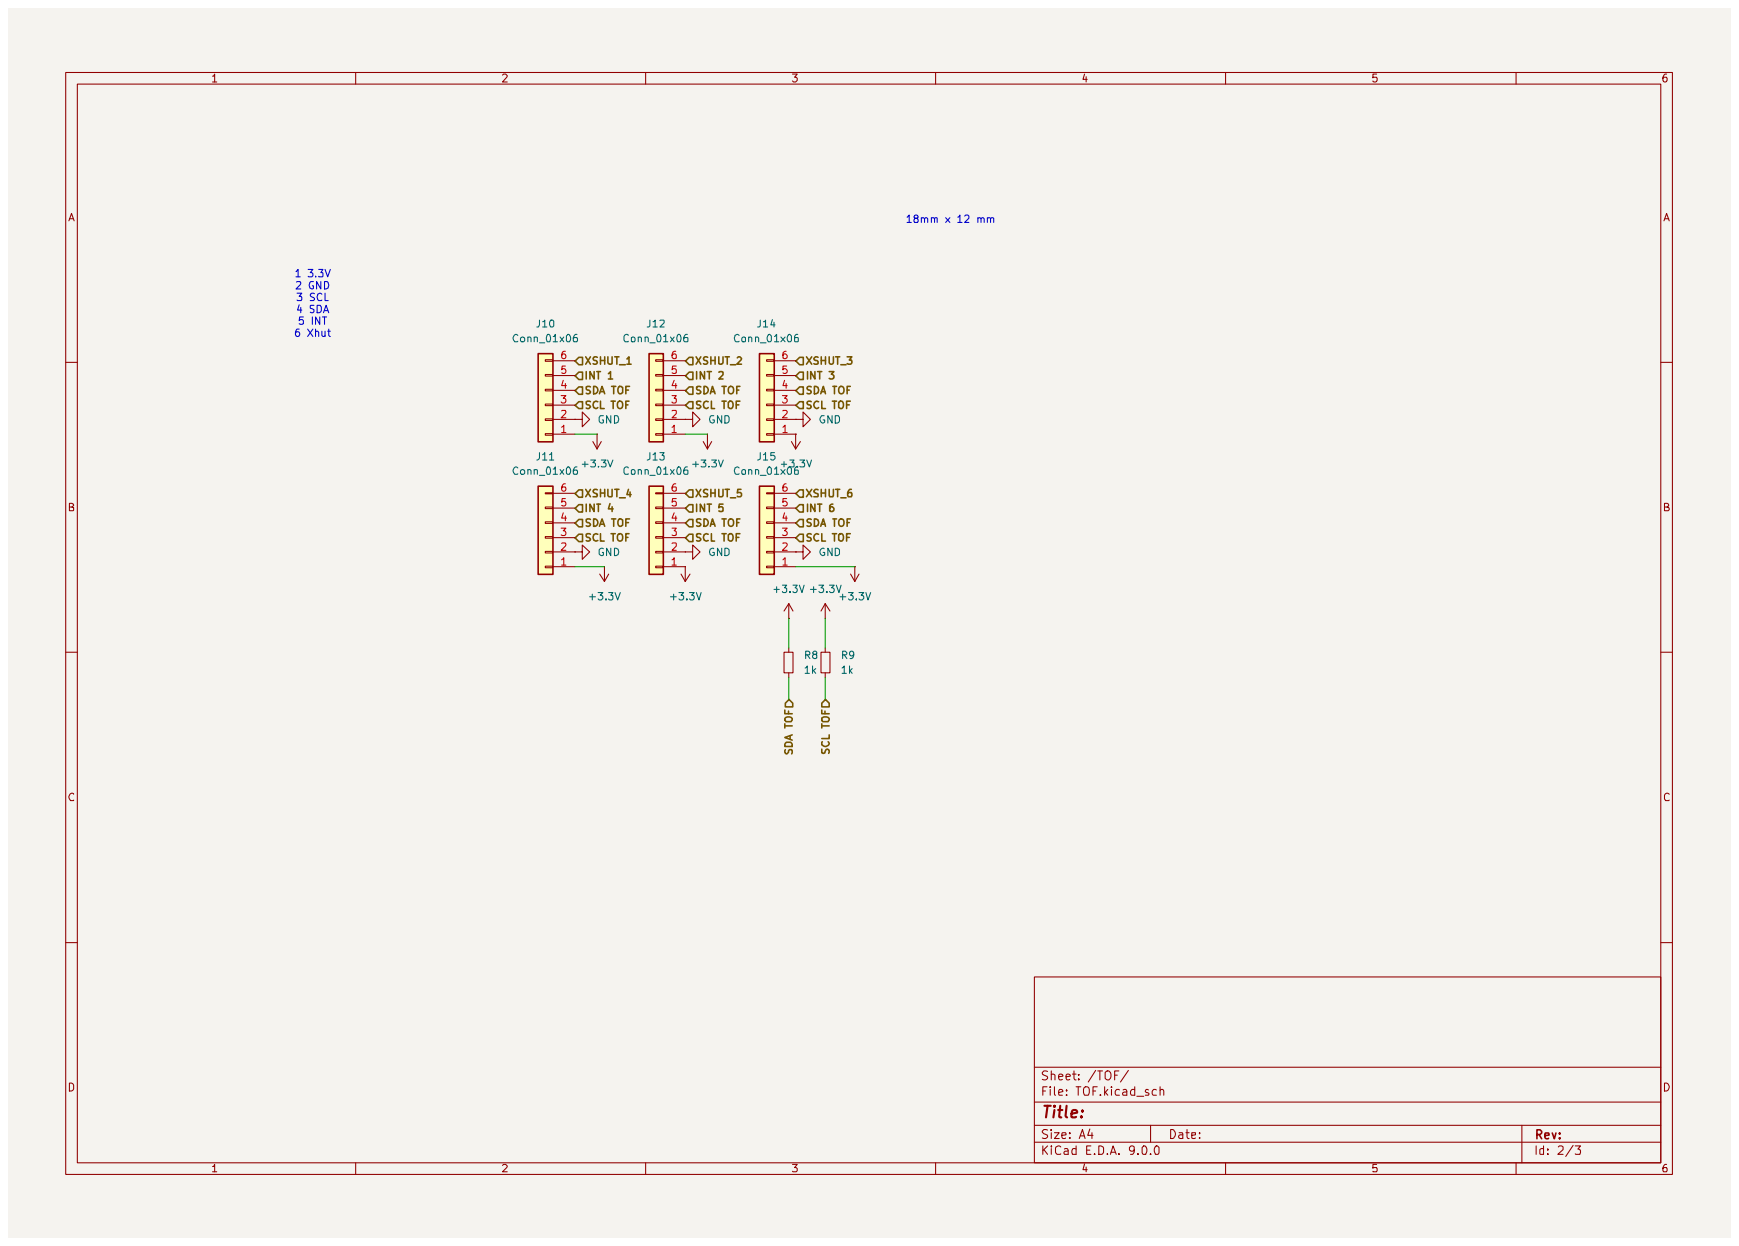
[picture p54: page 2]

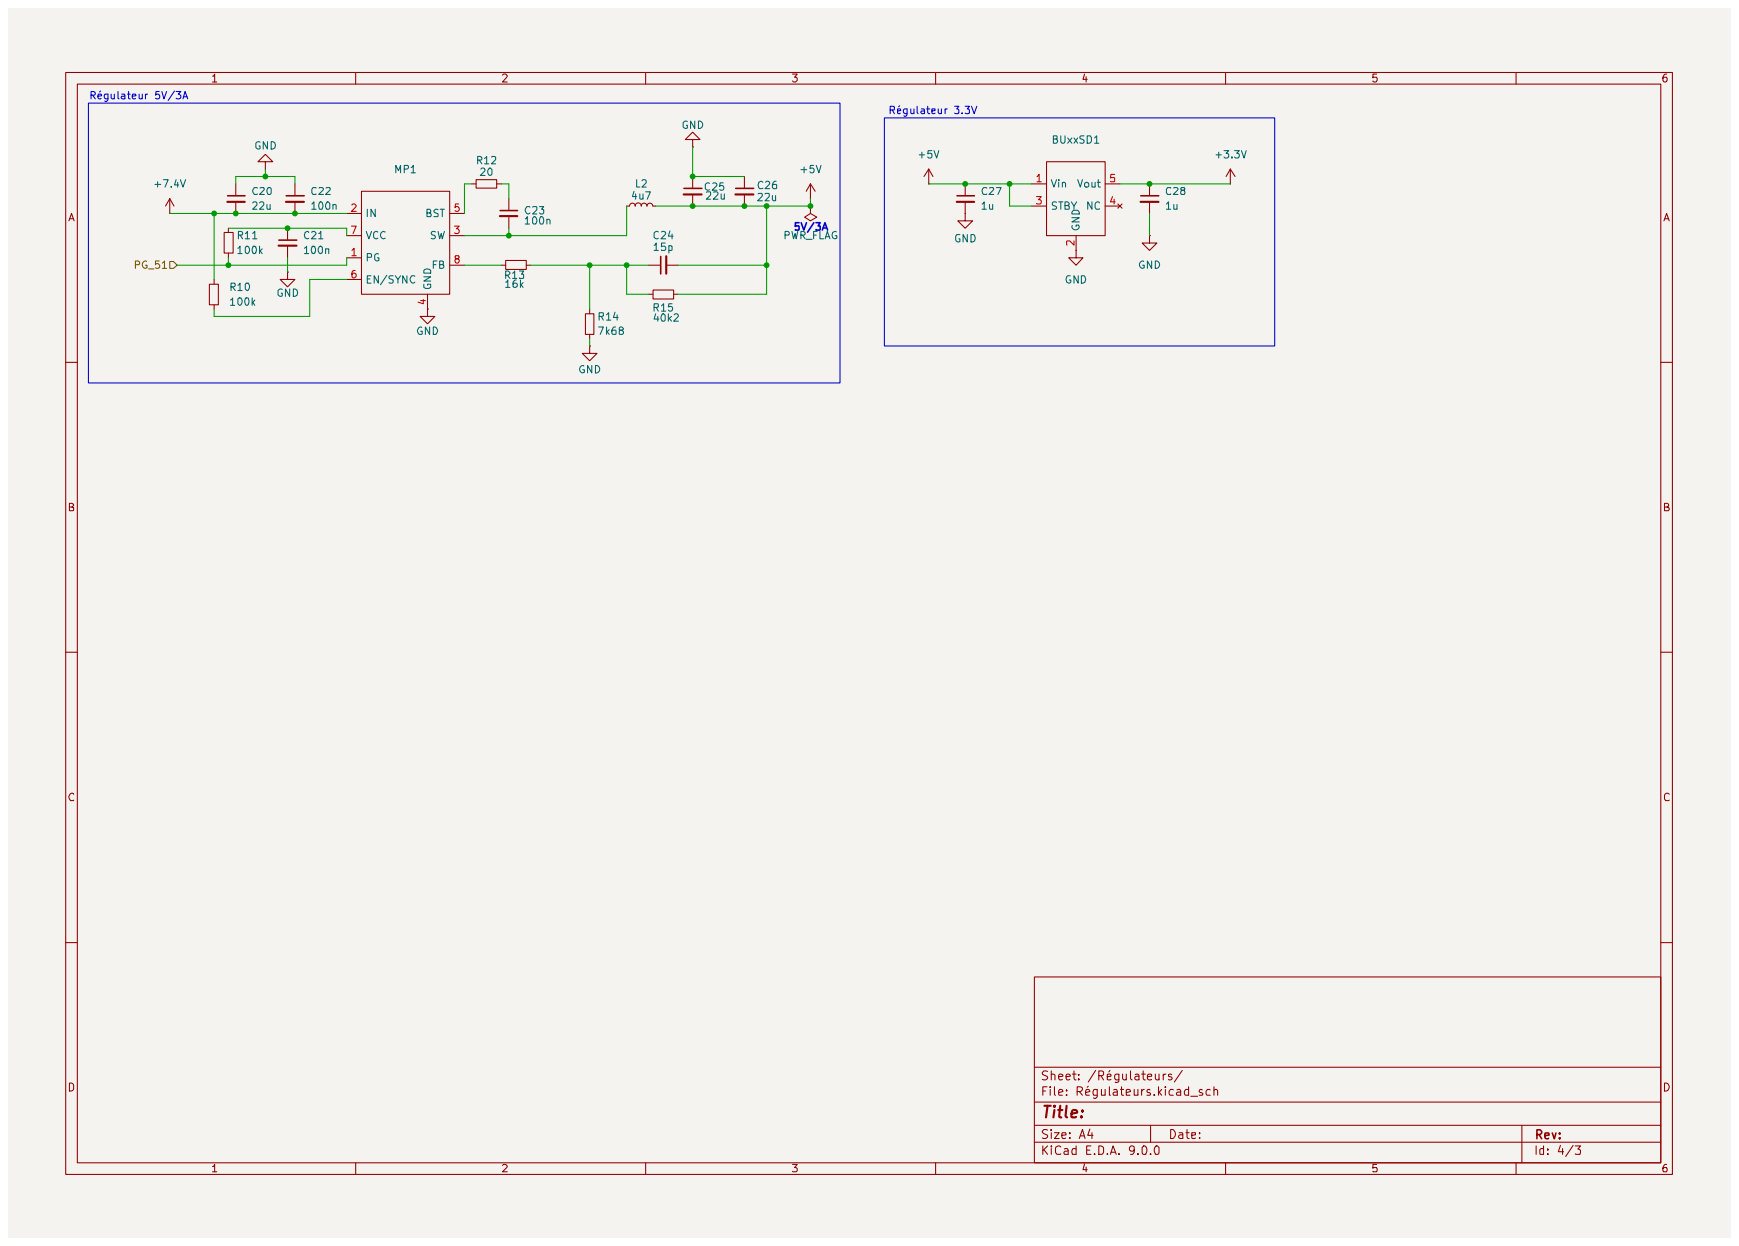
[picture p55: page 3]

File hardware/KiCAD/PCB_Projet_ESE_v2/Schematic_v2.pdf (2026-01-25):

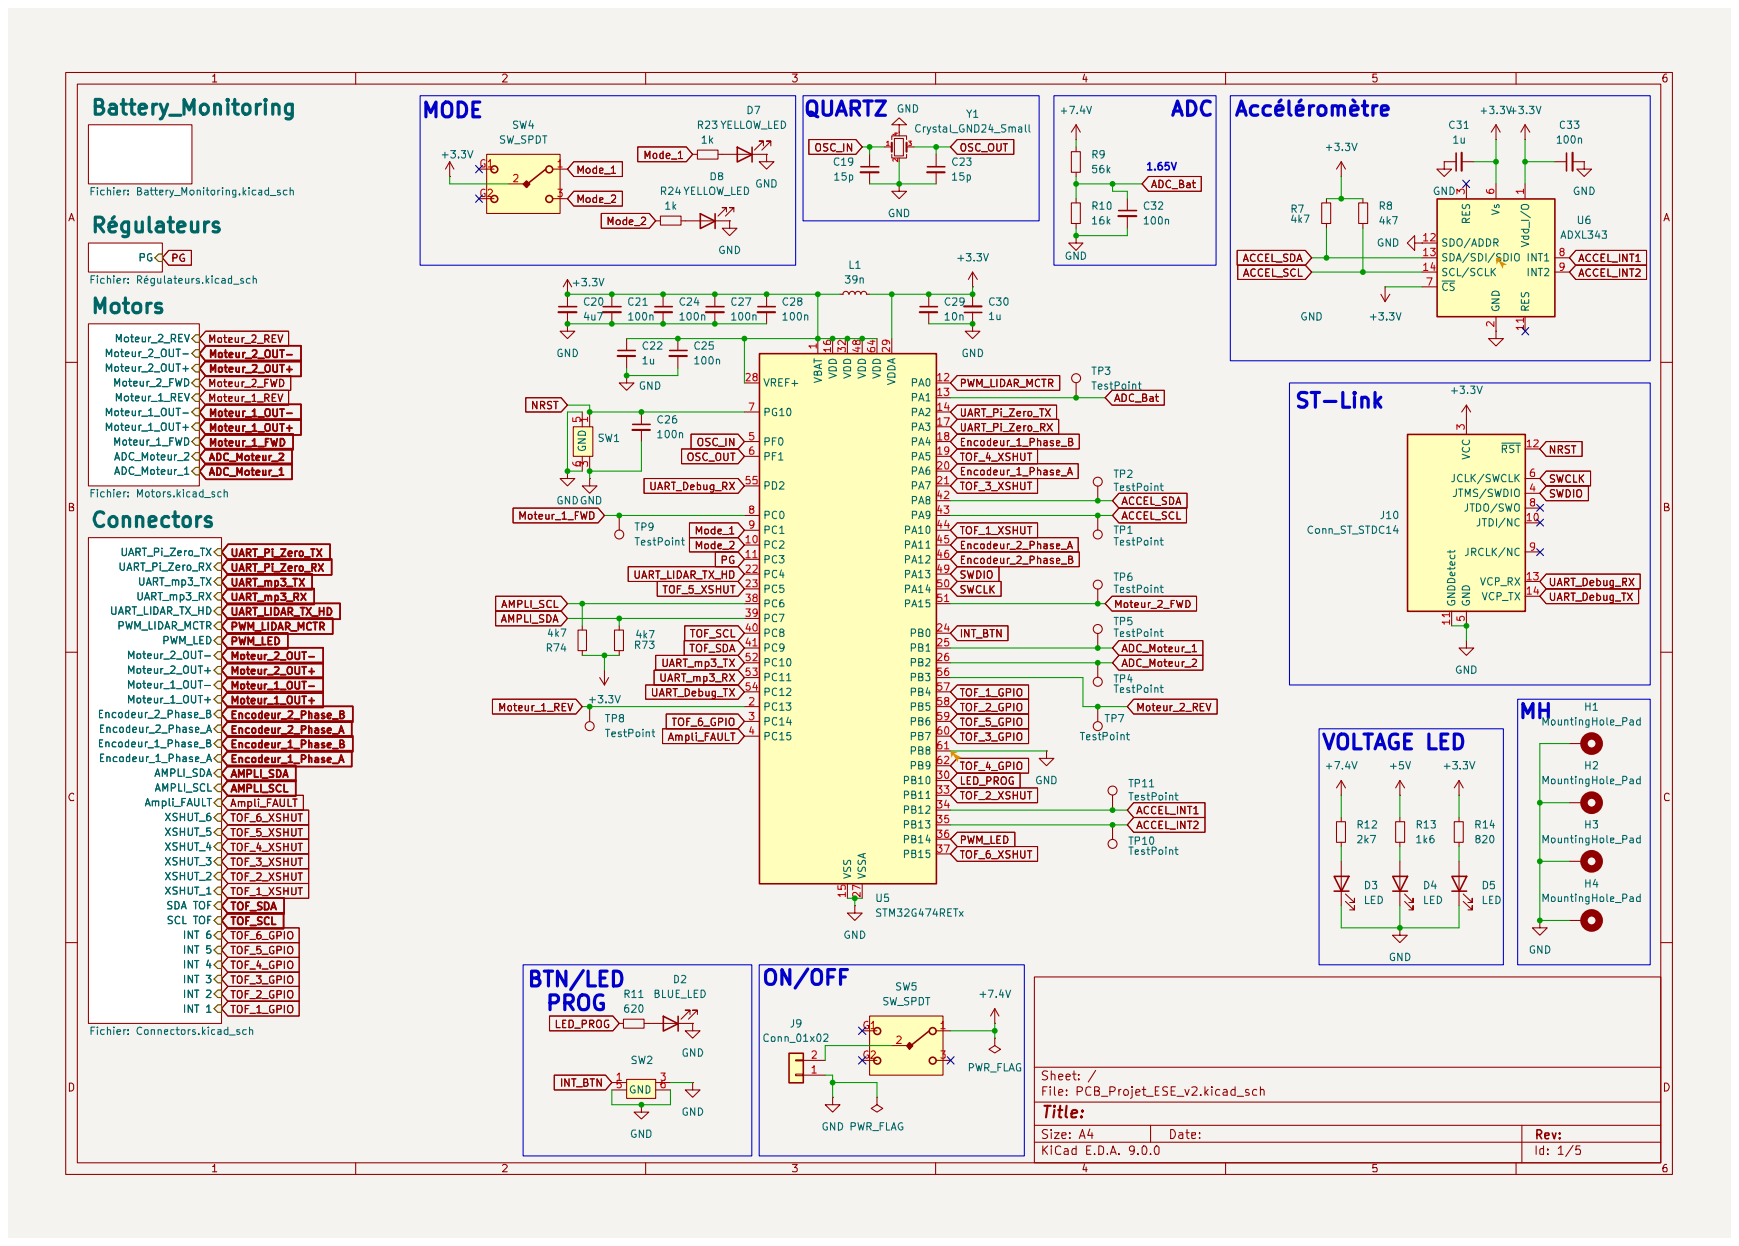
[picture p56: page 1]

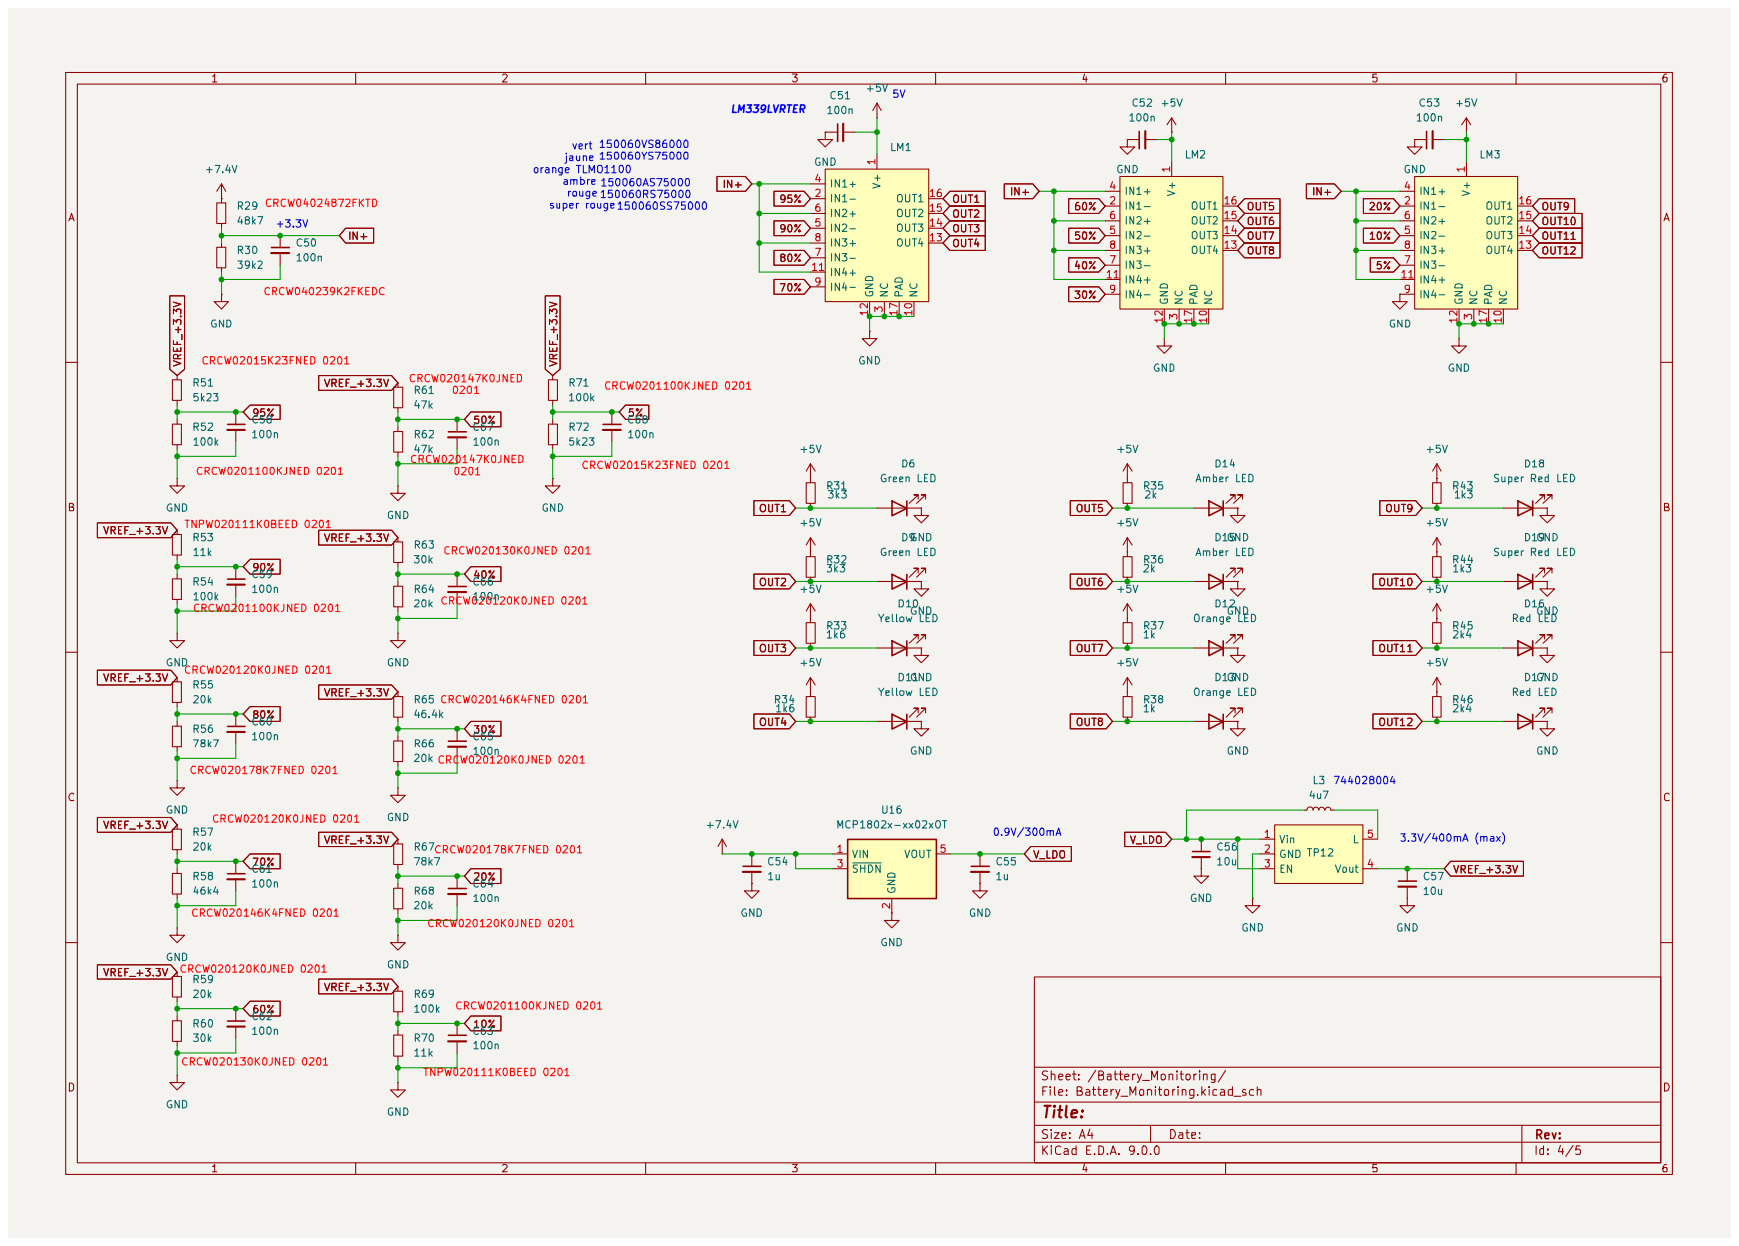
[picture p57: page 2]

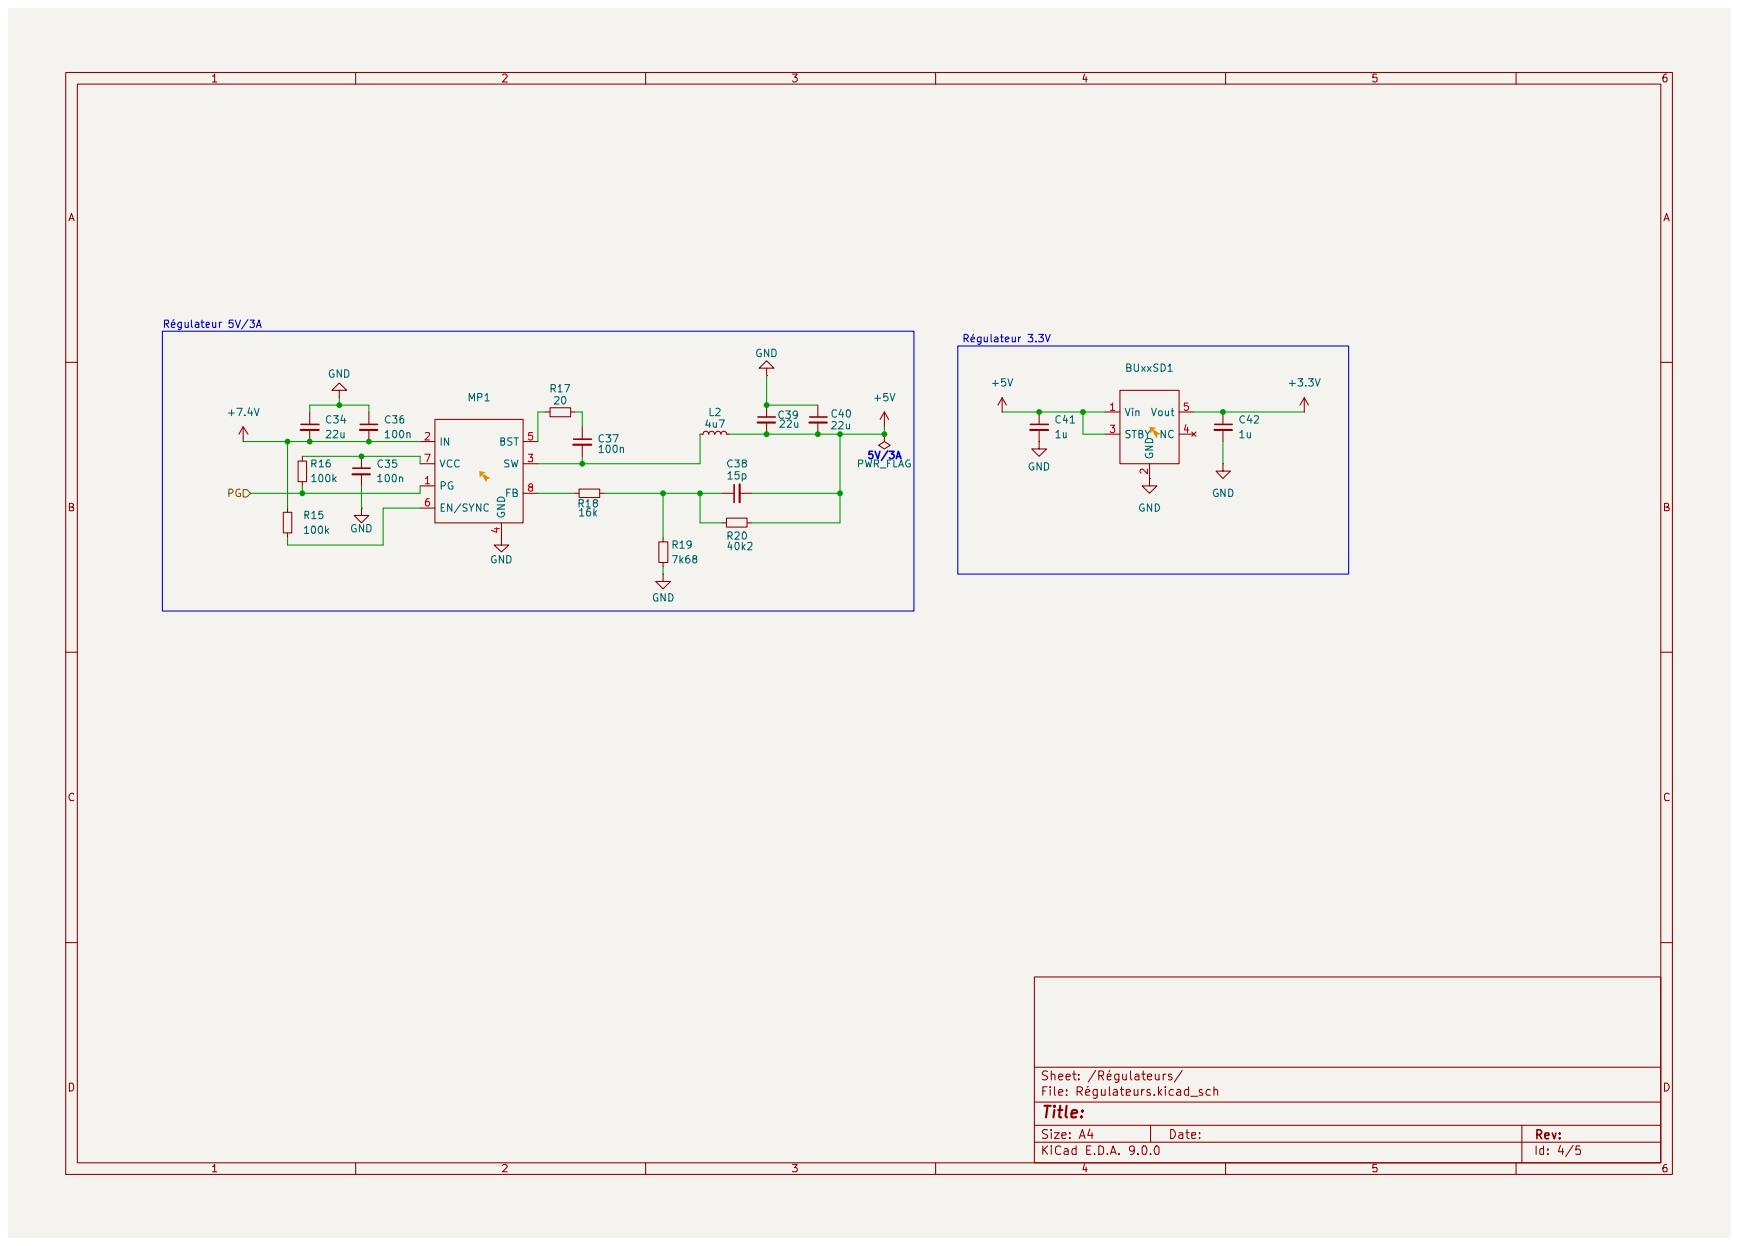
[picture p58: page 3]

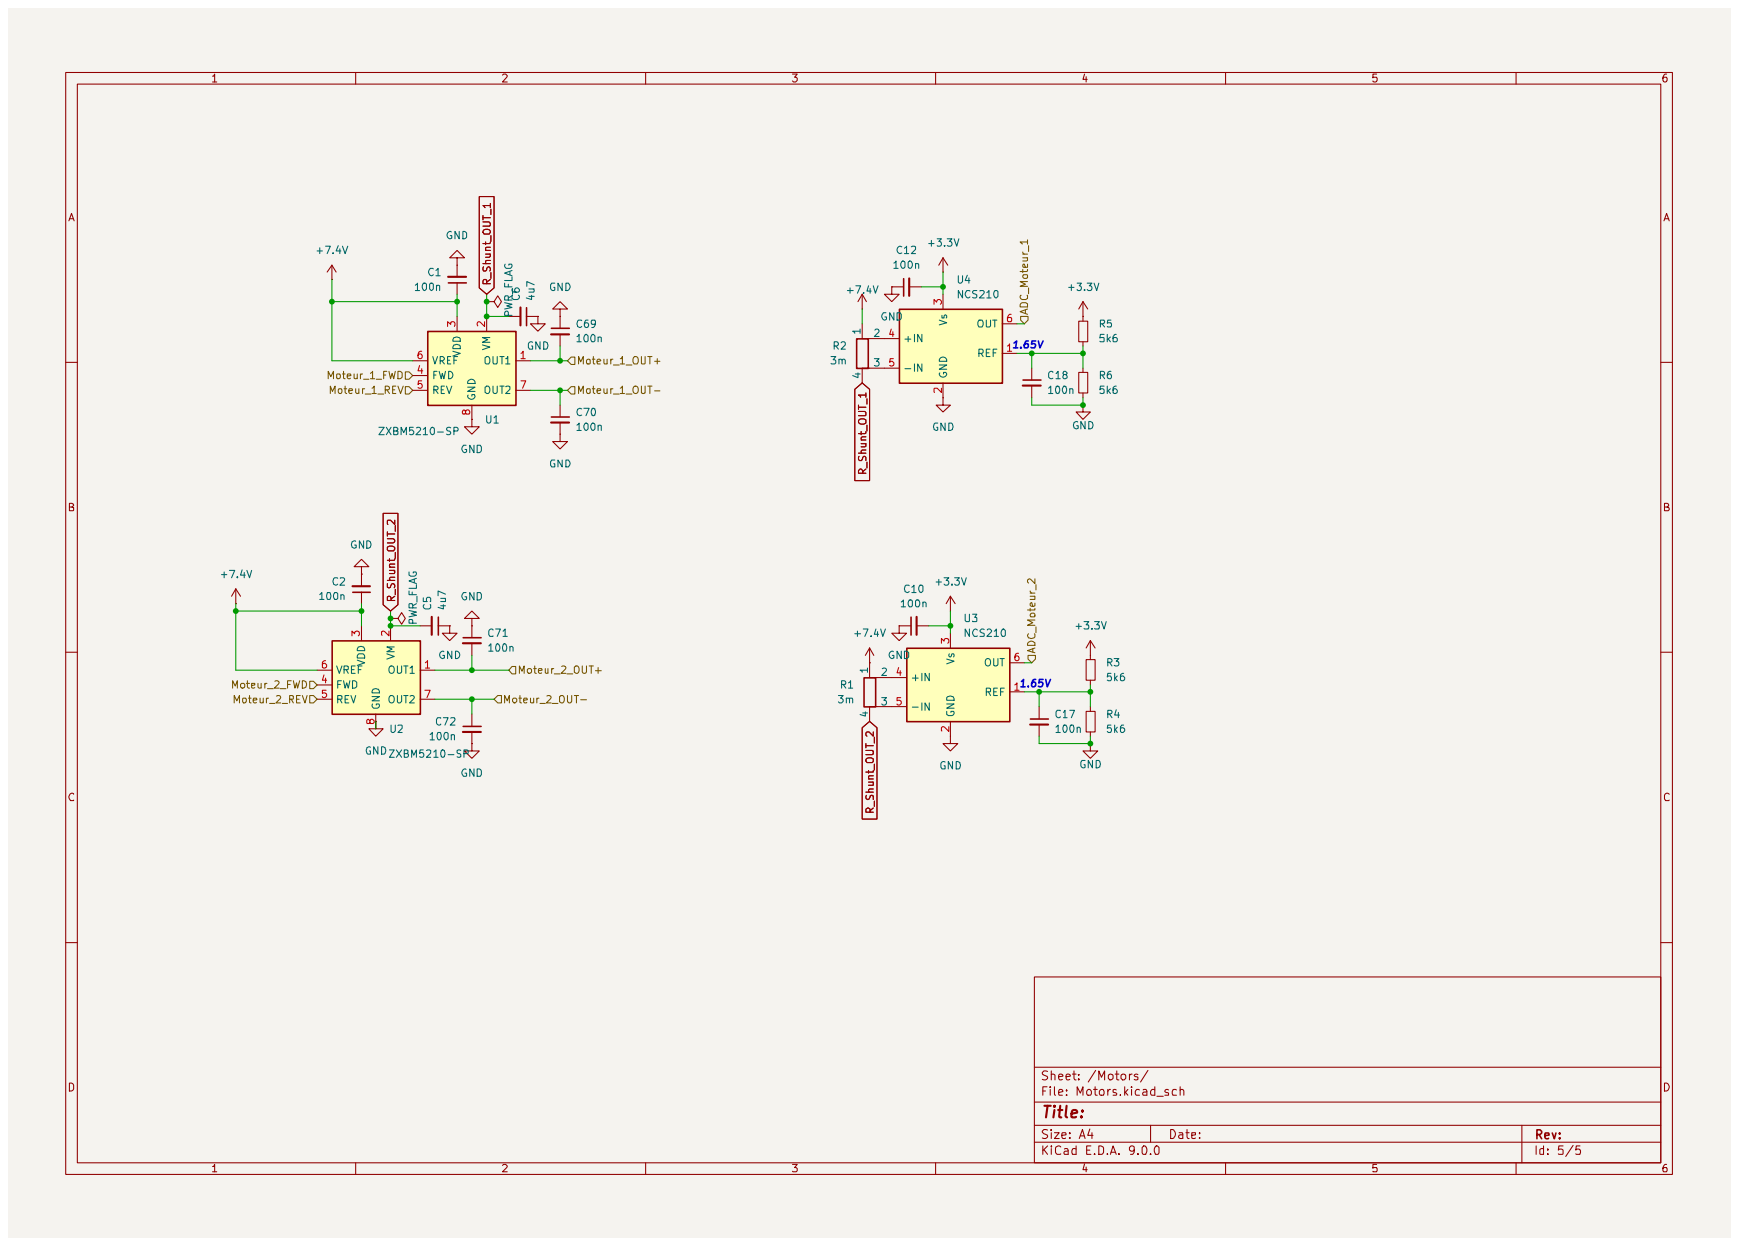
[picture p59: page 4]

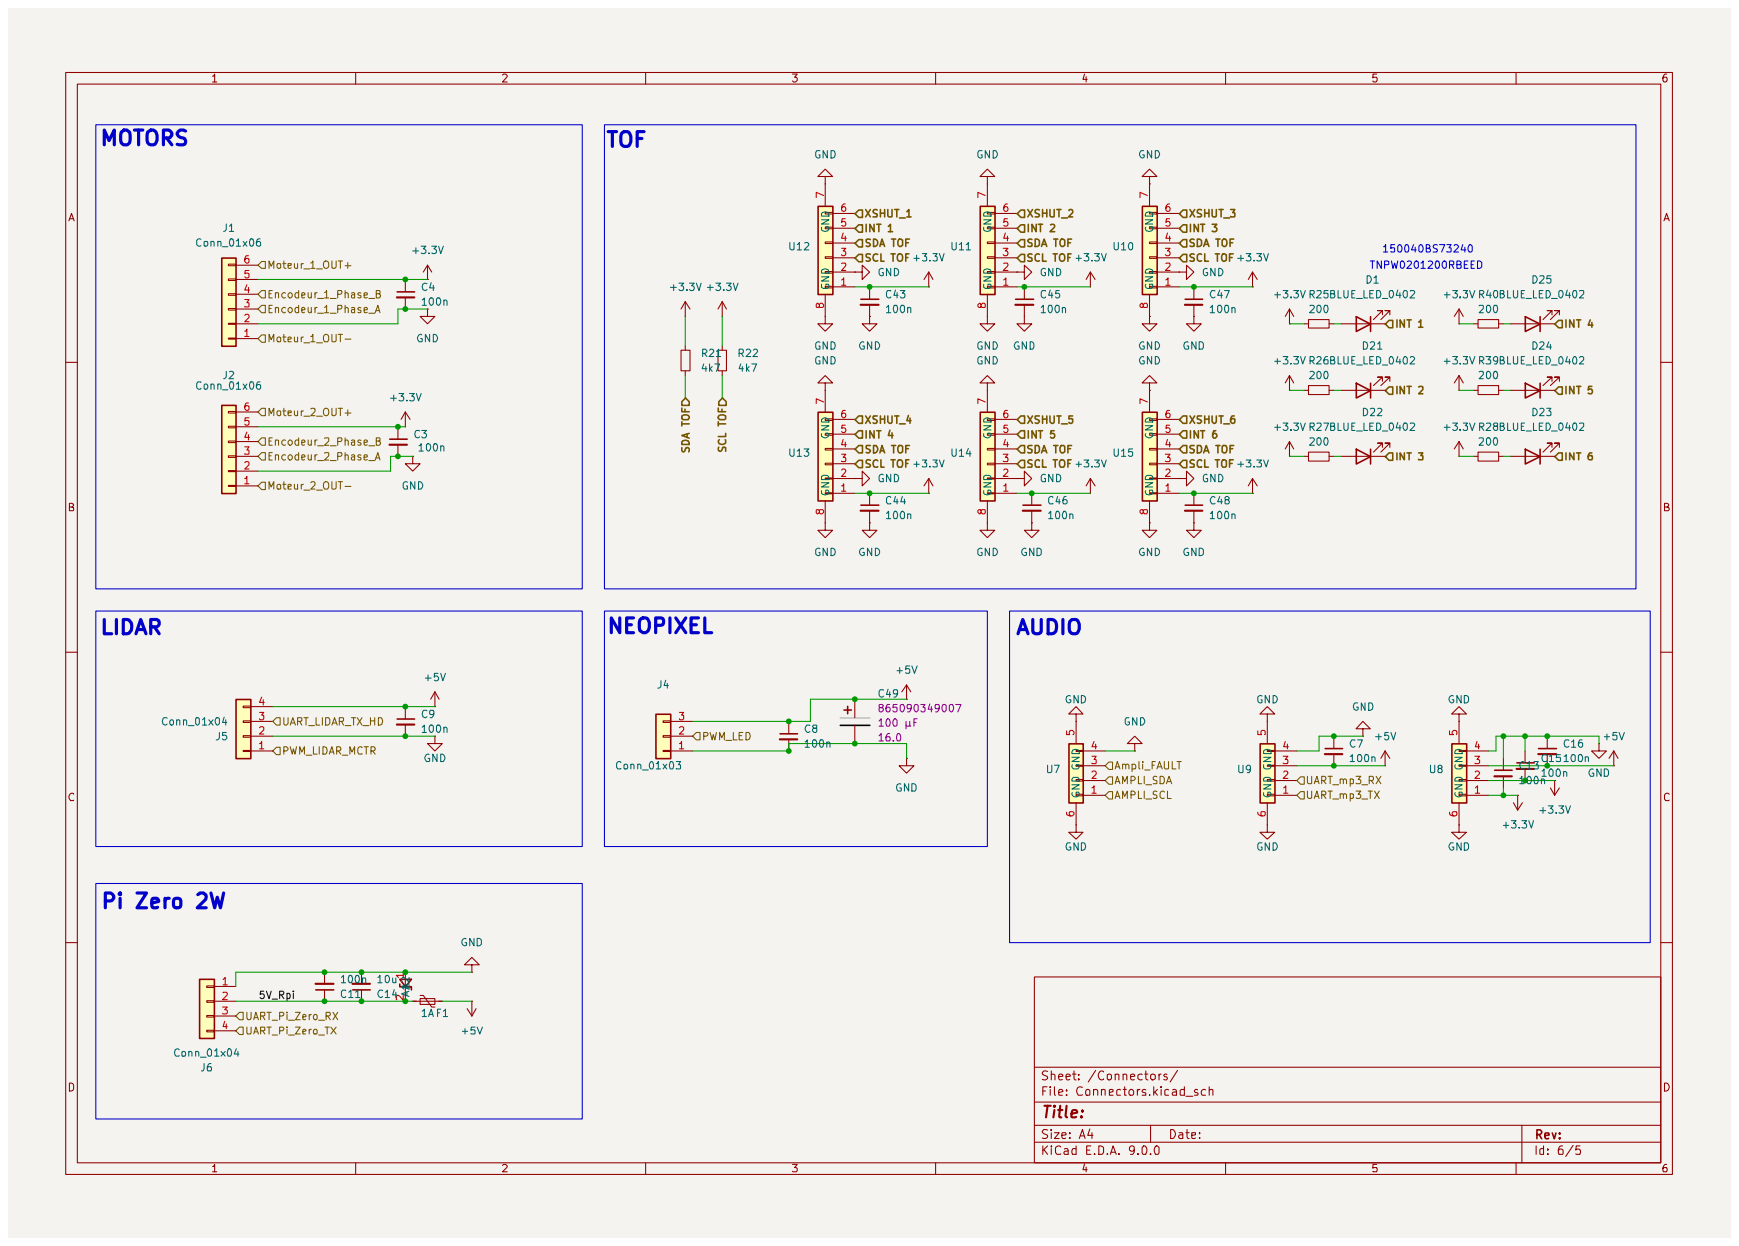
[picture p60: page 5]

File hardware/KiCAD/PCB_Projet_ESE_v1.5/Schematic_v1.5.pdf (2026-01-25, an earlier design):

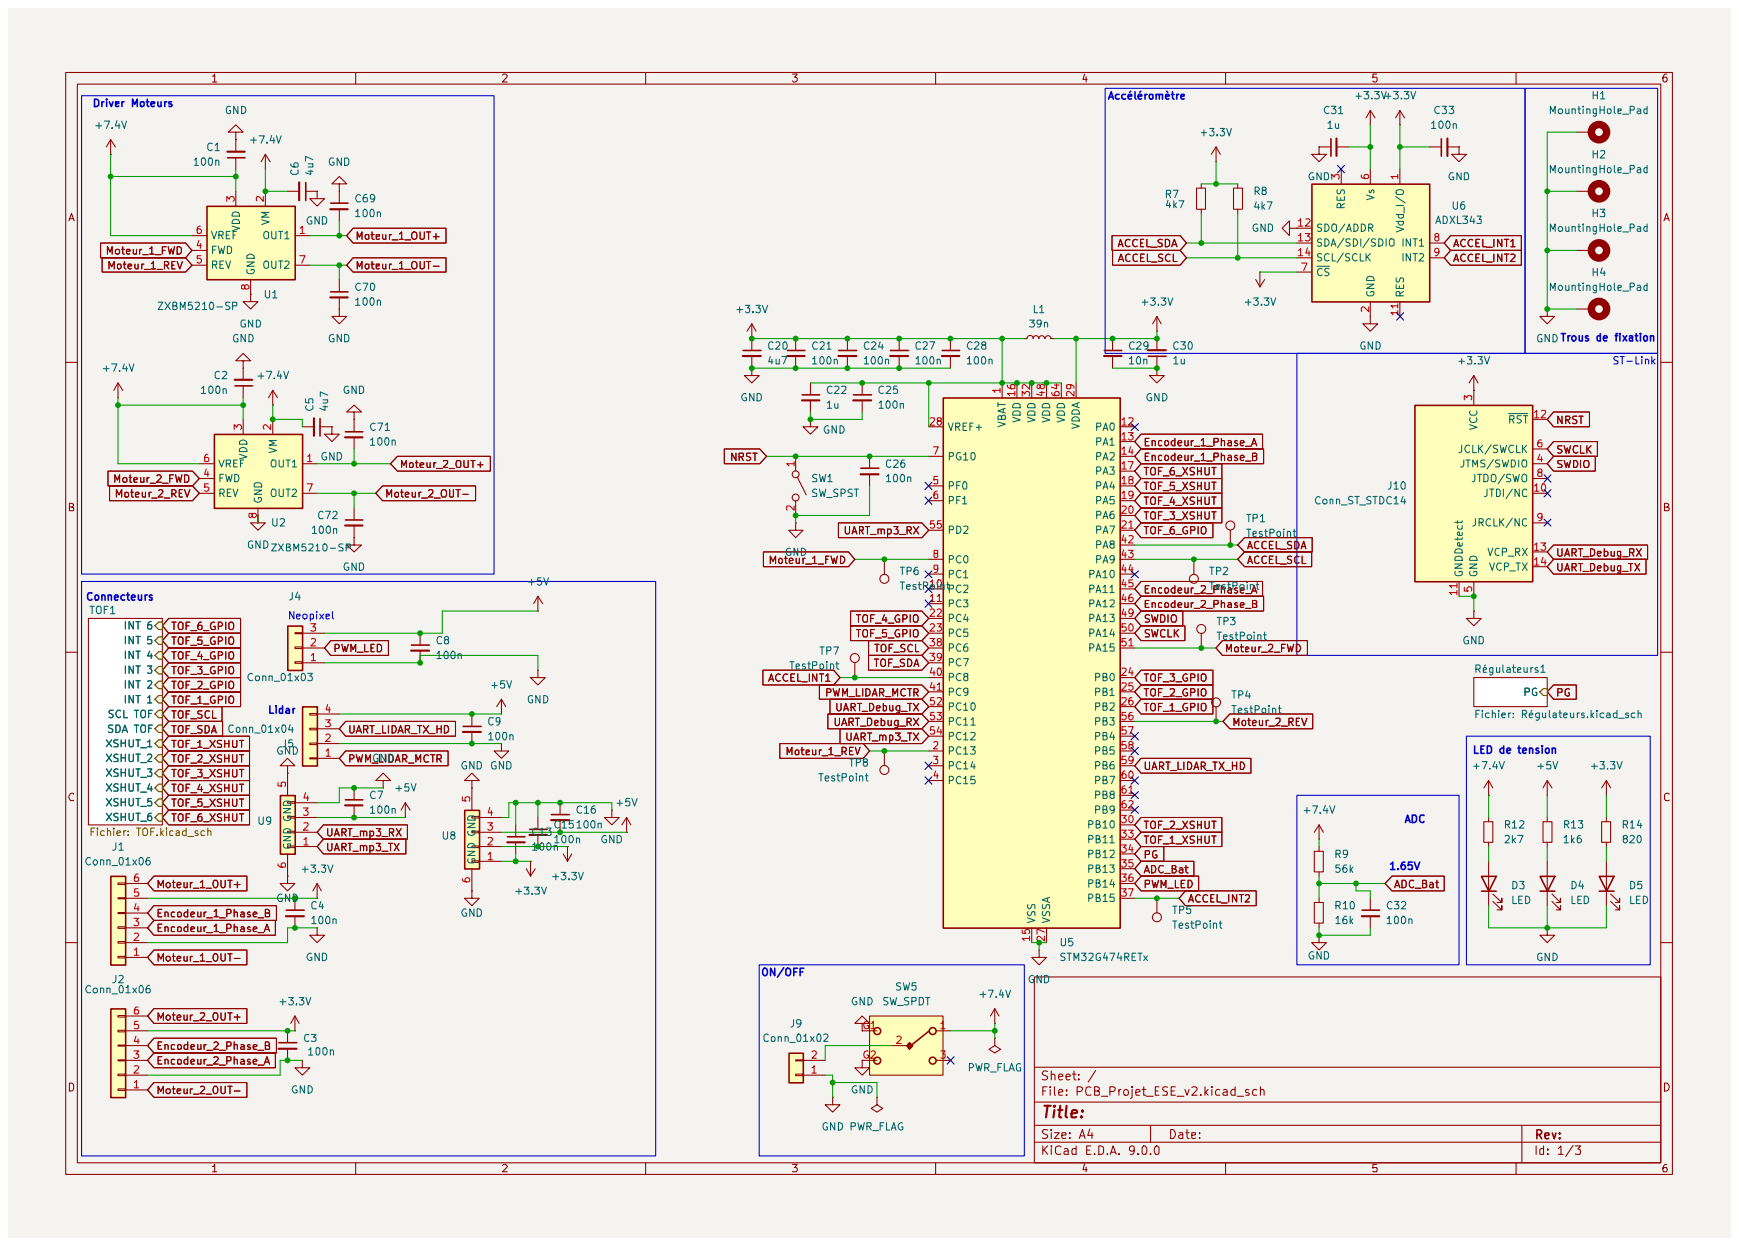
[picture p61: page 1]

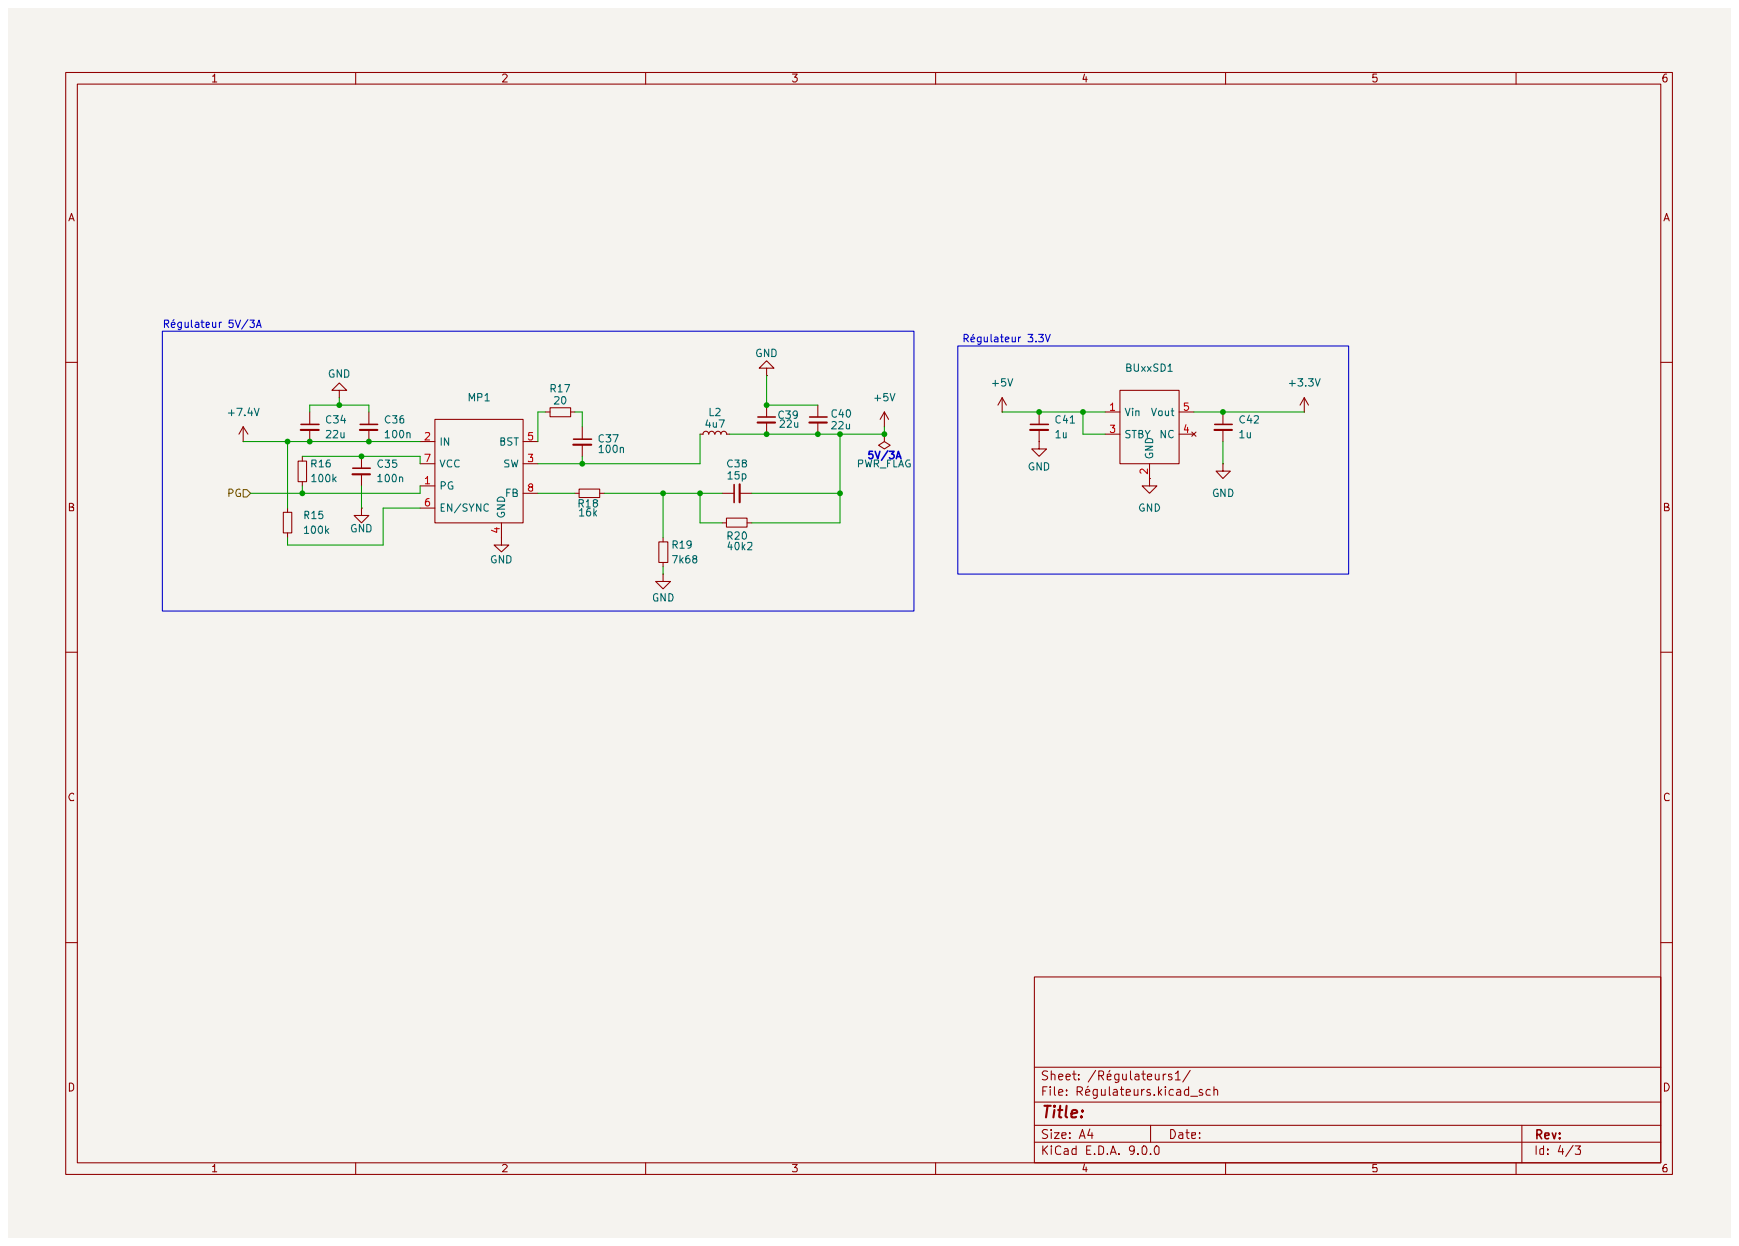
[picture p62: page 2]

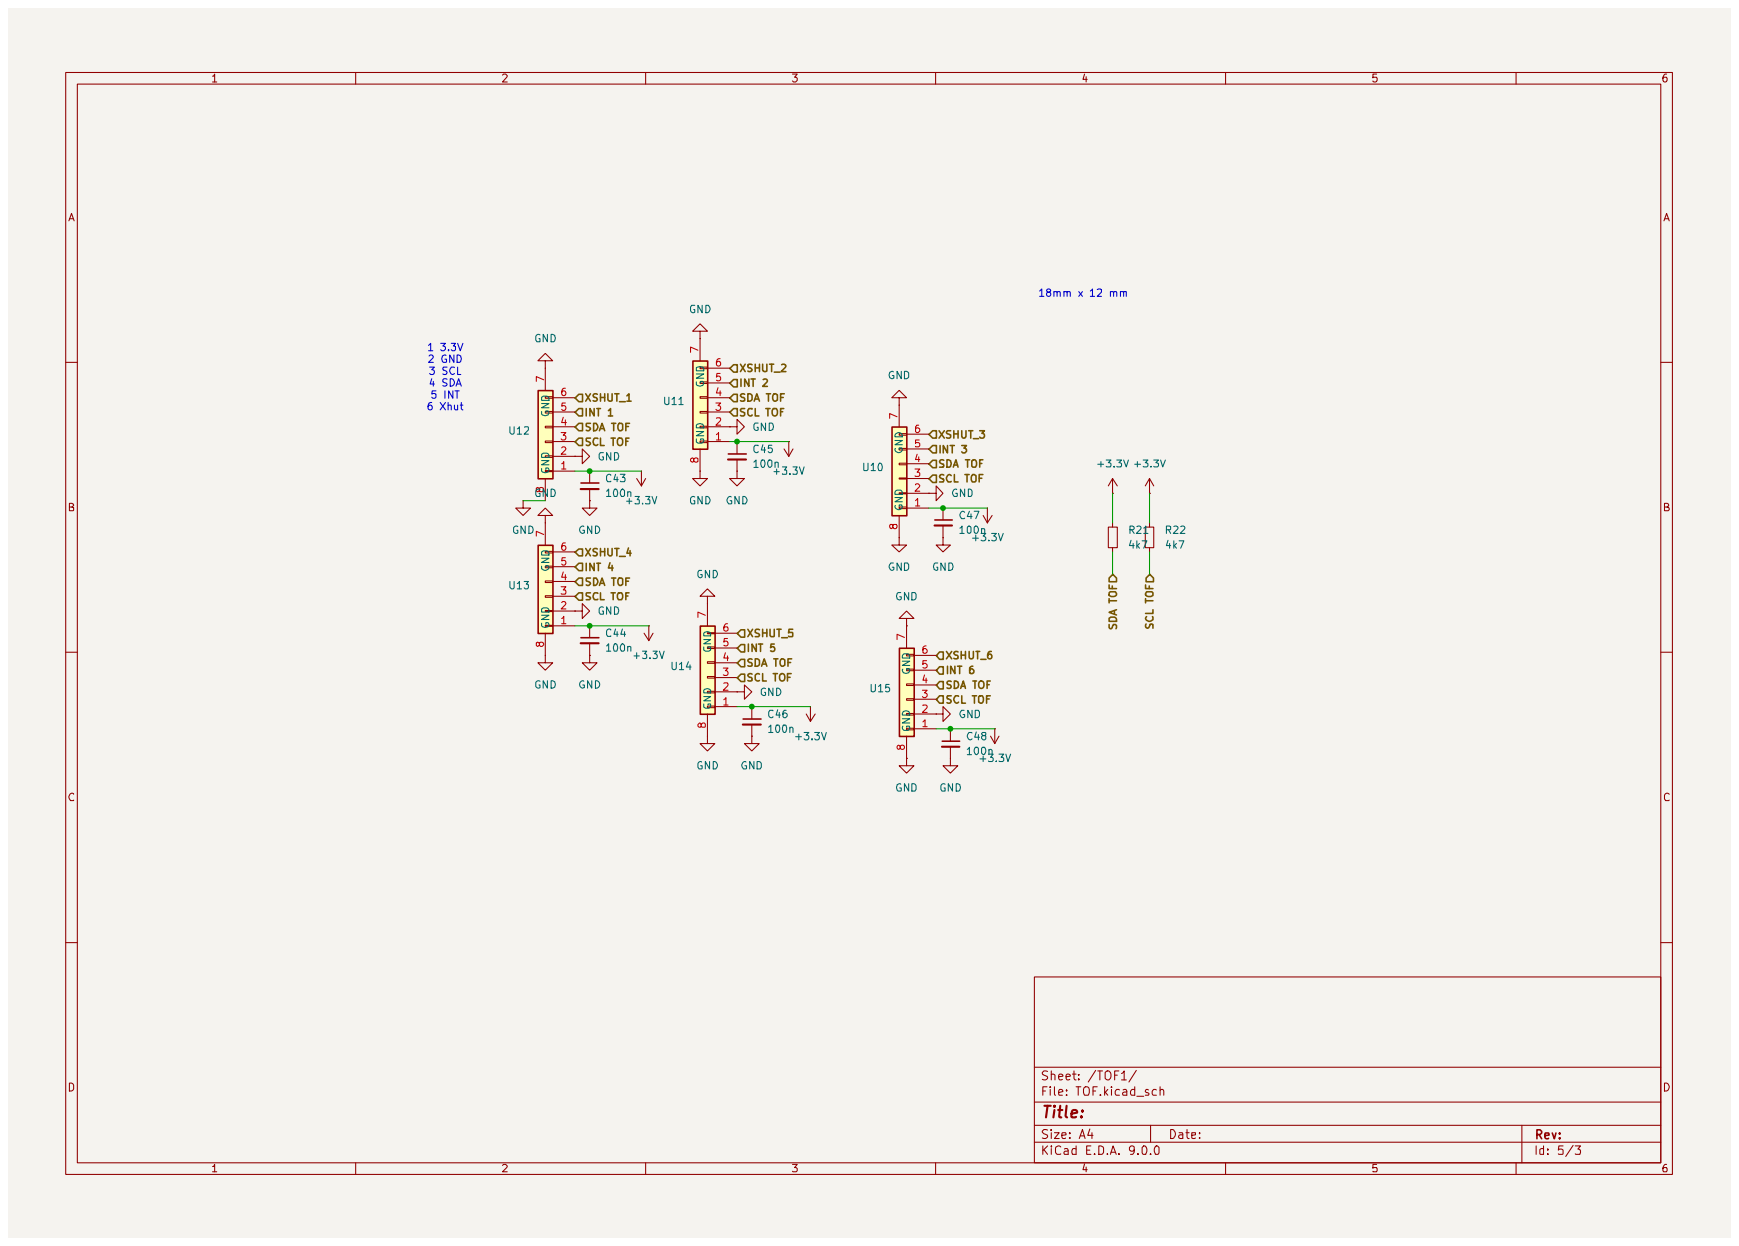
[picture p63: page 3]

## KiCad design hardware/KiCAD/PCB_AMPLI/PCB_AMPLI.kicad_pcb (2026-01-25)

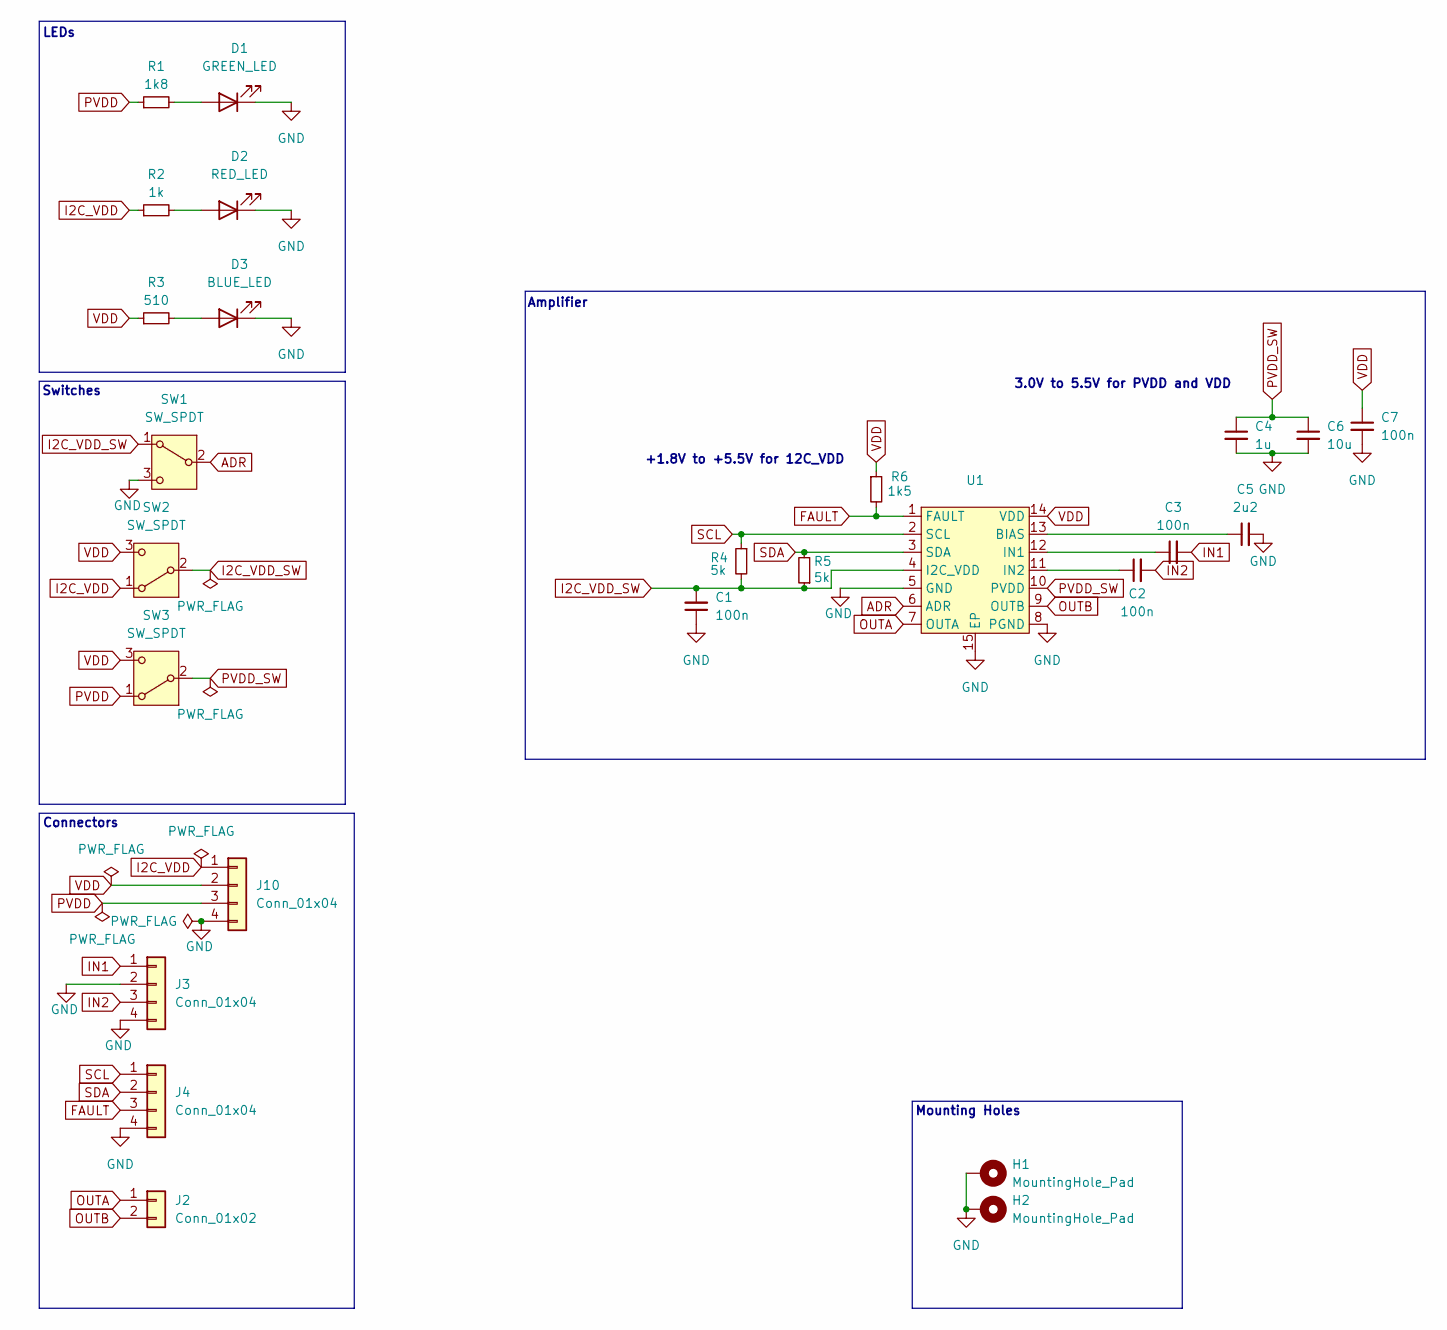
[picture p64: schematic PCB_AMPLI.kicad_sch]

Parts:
C1, C2, C3, C7: 100n; C_0402_1005Metric
C4: 1u; C_0603_1608Metric
C5: 2u2; C_0603_1608Metric
C6: 10u; C_0603_1608Metric
D1: GREEN_LED; LED_0603_1608Metric; MPN 150060GS55040
D2: RED_LED; LED_0603_1608Metric; MPN 150060RS55040
D3: BLUE_LED; LED_0603_1608Metric; MPN 150060BS55040
H1, H2: MountingHole_Pad; MountingHole_3.2mm_M3_Pad
J2: Conn_01x02; PinHeader_1x02_P2.54mm_Vertical
J3, J4, J10: Conn_01x04; PinHeader_1x04_P2.54mm_Vertical
R1: 1k8; R_0402_1005Metric
R2: 1k; R_0402_1005Metric
R3: 510; R_0402_1005Metric
R4, R5: 5k; R_0402_1005Metric
R6: 1k5; R_0402_1005Metric
SW1: SW_SPDT; 450406020024; MPN 450406020024
SW2, SW3: SW_SPDT; 450406020024
U1: HTSSOP-14-1EP_4.4x5mm_P0.65mm_EP3.4x5mm_Mask3x3.1mm; MPN LM48100QMHX/NOPB

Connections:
ADR: SW1.2 (B), U1.6 (ADR)
FAULT: J4.3, R6.2, U1.1 (FAULT)
GND: C1.1, C4.2, C5.2, C6.2, C7.2, D1.1 (K), D2.1 (K), D3.1 (K), H1.1, H2.1, J3.2, J3.4, J4.4, J10.4, SW1.3 (C), U1.5 (GND), U1.8 (PGND), U1.15 (EP)
I2C_VDD: J10.1, R2.1, SW2.1 (A)
I2C_VDD_SW: C1.2, R4.2, R5.1, SW1.1 (A), SW2.2 (B), U1.4 (I2C_VDD)
IN1: C3.2, J3.1
IN2: C2.2, J3.3
unnamed: D1.2 (A), R1.2
unnamed: D2.2 (A), R2.2
unnamed: D3.2 (A), R3.2
unnamed: C5.1, U1.13 (BIAS)
unnamed: C3.1, U1.12 (IN1)
unnamed: C2.1, U1.11 (IN2)
OUTA: J2.1, U1.7 (OUTA)
OUTB: J2.2, U1.9 (OUTB)
PVDD: J10.3, R1.1, SW3.1 (A)
PVDD_SW: C4.1, C6.1, SW3.2 (B), U1.10 (PVDD)
SCL: J4.1, R4.1, U1.2 (SCL)
SDA: J4.2, R5.2, U1.3 (SDA)
VDD: C7.1, J10.2, R3.1, R6.1, SW2.3 (C), SW3.3 (C), U1.14 (VDD)

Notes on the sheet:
+1.8V to +5.5V for 12C_VDD
Mounting Holes
Switches
3.0V to 5.5V for PVDD and VDD
LEDs
Connectors
Amplifier

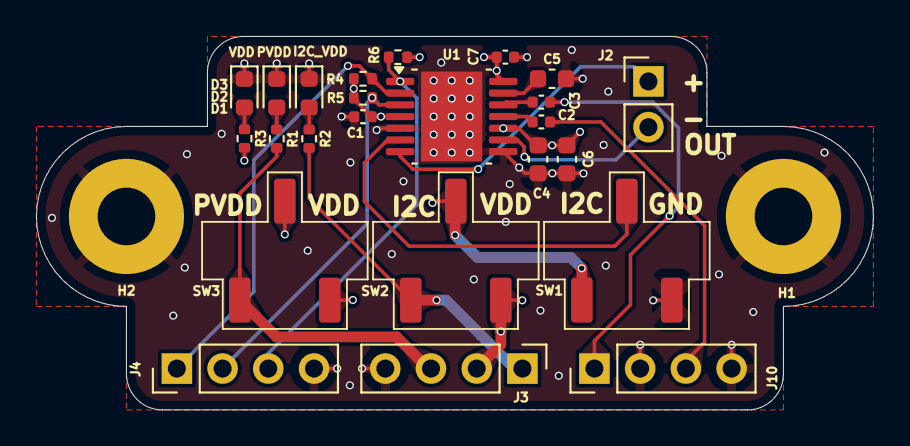
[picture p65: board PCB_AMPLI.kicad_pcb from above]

Board: 4 copper layers, 46.5 x 20.8 mm, 26 parts (0 on the bottom side), 20 nets.

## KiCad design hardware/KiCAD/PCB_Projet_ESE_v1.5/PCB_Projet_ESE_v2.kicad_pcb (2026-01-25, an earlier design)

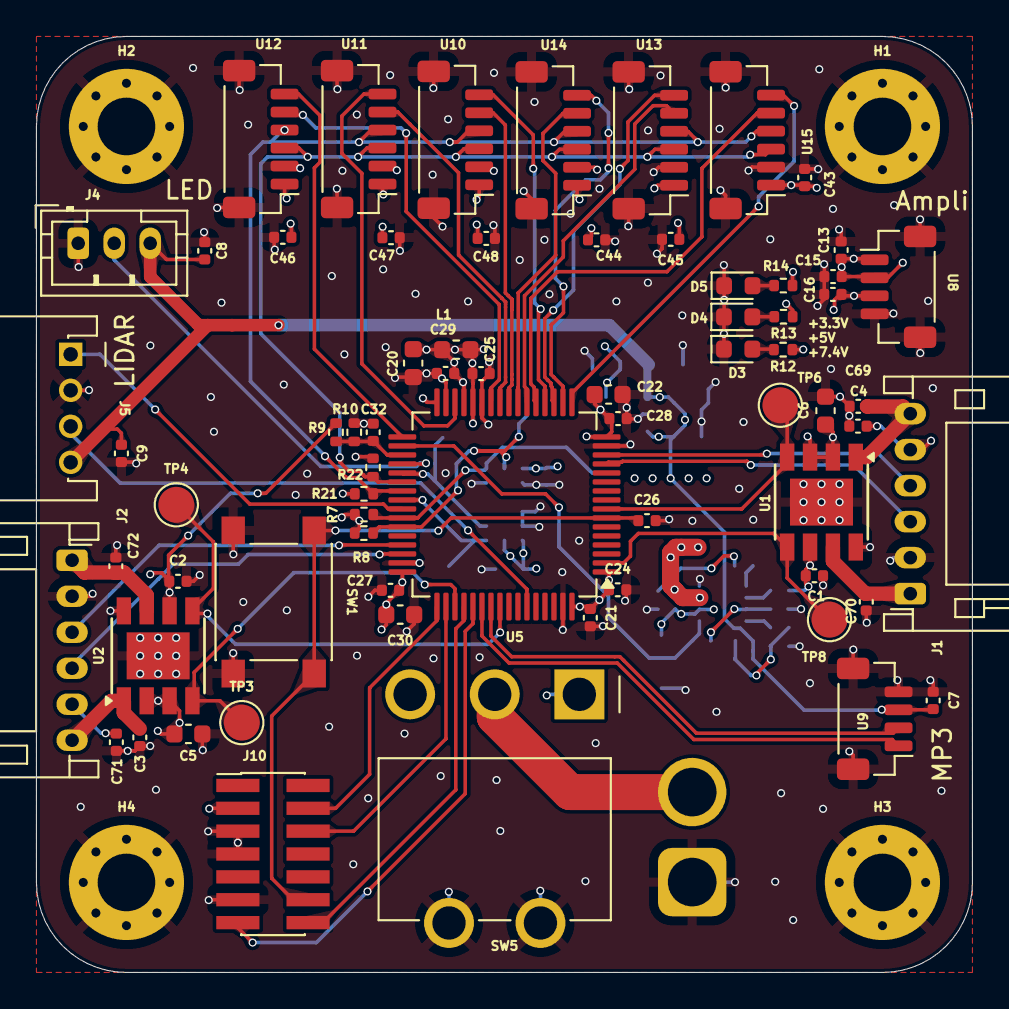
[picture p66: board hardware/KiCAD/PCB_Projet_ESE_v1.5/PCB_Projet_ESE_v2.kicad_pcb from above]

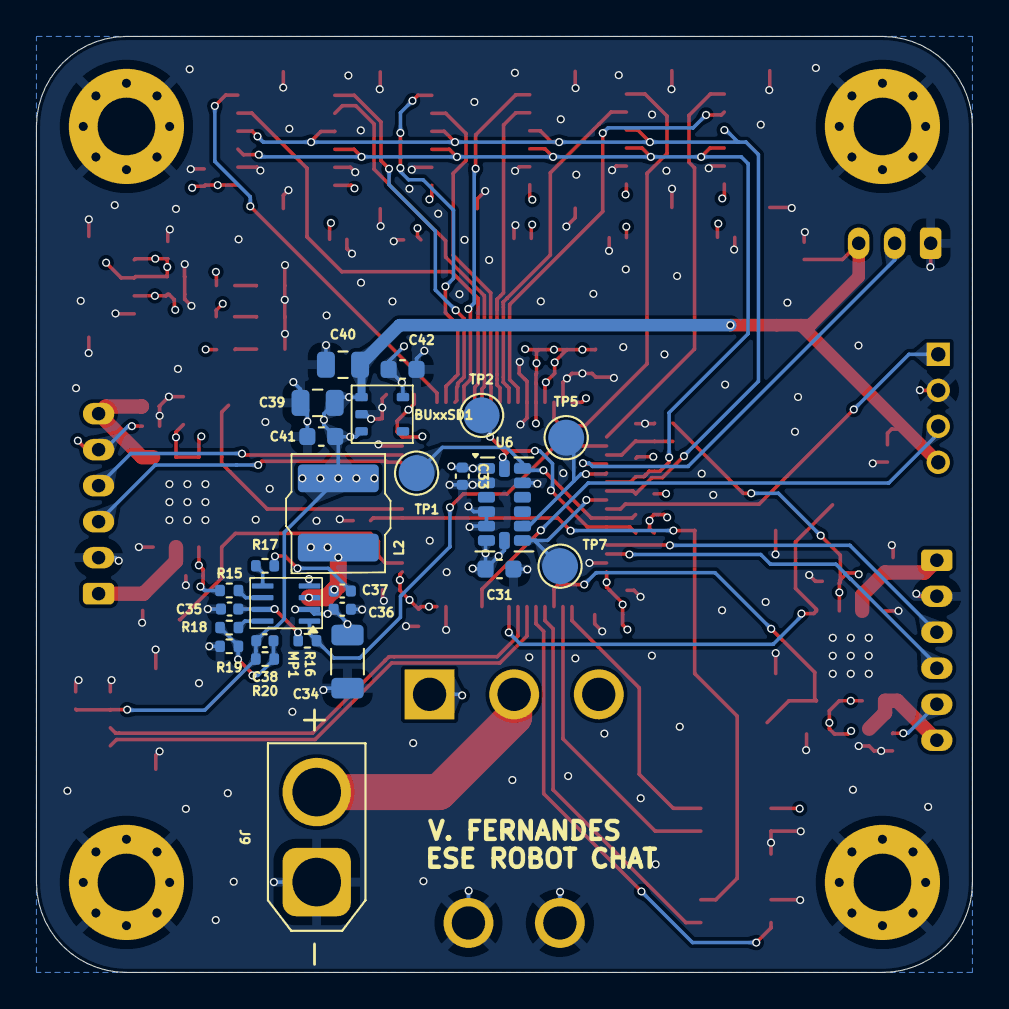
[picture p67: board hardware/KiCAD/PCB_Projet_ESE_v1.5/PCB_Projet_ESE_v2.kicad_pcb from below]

Board: 4 copper layers, 52.0 x 52.0 mm, 98 parts (26 on the bottom side), 57 nets.

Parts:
BUxxSD1: SSOP5_BUxxSD5
C1, C2, C3, C4, C7, C8, C9, C13, C15, C16, C21, C24, C25, C26, C27, C28, C32, C33, C35, C36, C37, C43, C44, C45, C46, C47, C48, C69, C70, C71, C72: 100n; C_0402_1005Metric
C5, C6, C20: 4u7; C_0603_1608Metric
C22, C30, C31, C41, C42: 1u; C_0603_1608Metric
C29: 10n; C_0402_1005Metric
C34: 22u; C_1206_3216Metric
C38: 15p; C_0402_1005Metric
C39, C40: 22u; C_0805_2012Metric
D3, D4, D5: LED; LED_0603_1608Metric
H1, H2, H3, H4: MountingHole_Pad; MountingHole_3.2mm_M3_Pad_Via
J1, J2: Conn_01x06; JST_PH_S6B-PH-K_1x06_P2.00mm_Horizontal
J4: Conn_01x03; JST_PH_B3B-PH-K_1x03_P2.00mm_Vertical
J5: Conn_01x04; J_Wurth_WR-WTB_62000411722
J9: Conn_01x02; AMASS_XT30U-M_1x02_P5.0mm_Vertical
J10: Conn_ST_STDC14; PinHeader_2x07_P1.27mm_Vertical_SMD
L1: 39n; L_0603_1608Metric
L2: 4u7; 74404054068
MP1: TSOT23-8
R7, R8, R21, R22: 4k7; R_0402_1005Metric
R9: 56k; R_0402_1005Metric
R10, R18: 16k; R_0402_1005Metric
R12: 2k7; R_0402_1005Metric
R13: 1k6; R_0402_1005Metric
R14: 820; R_0402_1005Metric
R15, R16: 100k; R_0402_1005Metric
R17: 20; R_0402_1005Metric
R19: 7k68; R_0402_1005Metric
R20: 40k2; R_0402_1005Metric
SW1: SW_SPST
SW5: SW_SPDT; SW_Wurth_WS-TOTV_472123020421
TP1, TP2, TP3, TP4, TP5, TP6, TP7, TP8: TestPoint; TestPoint_Pad_D2.0mm
U1, U2: ZXBM5210-SP; Diodes_SO-8EP
U5: STM32G474RETx; LQFP-64_10x10mm_P0.5mm
U6: ADXL343; LGA-14_3x5mm_P0.8mm_LayoutBorder1x6y
U8, U9: JST_SH_4_Vertical
U10, U11, U12, U13, U14, U15: JST_SH_6_Vertical

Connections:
+3.3V: BUxxSD1.5 (Vout), C3.1, C4.1, C13.2, C15.2, C20.1, C21.1, C22.1, C24.1, C25.1, C27.1, C28.1, C29.1, C30.2, C31.2, C33.1, C42.1, C43.1, C44.1, C45.1, C46.1, C47.1, C48.1, J1.5, J2.5, J10.3 (VCC), L1.1, L1.2, R7.1, R8.1, R14.1, R21.1, R22.1, U5.1 (VBAT), U5.16 (VDD), U5.28 (VREF+), U5.29 (VDDA), U5.32 (VDD), U5.48 (VDD), U5.64 (VDD), U6.1 (Vdd_I/O), U6.6 (Vs), U6.7 (~CS), U8.1, U8.2, U10.1, U11.1, U12.1, U13.1, U14.1, U15.1
+5V: BUxxSD1.1 (Vin), BUxxSD1.3 (STBY), C7.2, C8.1, C9.1, C16.2, C38.2, C39.2, C40.2, C41.1, J4.3, J5.4, L2.2, R13.1, R20.2, U8.3, U9.3
+7.4V: C1.1, C2.1, C5.2, C6.2, C34.2, C36.2, MP1.2 (IN), R9.1, R12.1, R15.1, SW5.1, U1.2 (VM), U1.3 (VDD), U1.6 (VREF), U2.2 (VM), U2.3 (VDD), U2.6 (VREF)
ACCEL_INT1: TP7.1, U5.40 (PC8), U6.8 (INT1)
ACCEL_INT2: TP5.1, U5.37 (PB15), U6.9 (INT2)
ACCEL_SCL: R8.2, TP2.1, U5.43 (PA9), U6.14 (SCL/SCLK)
ACCEL_SDA: R7.2, TP1.1, U5.42 (PA8), U6.13 (SDA/SDI/SDIO)
ADC_Bat: C32.1, R9.2, R10.1, U5.35 (PB13)
Encodeur_1_Phase_A: J1.3, U5.13 (PA1)
Encodeur_1_Phase_B: J1.4, U5.14 (PA2)
Encodeur_2_Phase_A: J2.3, U5.45 (PA11)
Encodeur_2_Phase_B: J2.4, U5.46 (PA12)
GND: BUxxSD1.2 (GND), C1.2, C2.2, C3.2, C4.2, C5.1, C6.1, C7.1, C8.2, C9.2, C13.1, C15.1, C16.1, C20.2, C21.2, C22.2, C24.2, C25.2, C26.2, C27.2, C28.2, C29.2, C30.1, C31.1, C32.2, C33.2, C34.1, C35.2, C36.1, C39.1, C40.1, C41.2, C42.2, C43.2, C44.2, C45.2, C46.2, C47.2, C48.2, C69.1, C70.2, C71.1, C72.2, D3.1 (K), D4.1 (K), D5.1 (K), H1.1, H2.1, H3.1, H4.1, J1.2, J2.2, J4.1, J5.2, J9.1, J10.5 (GND), J10.7 (GND), J10.11 (GNDDetect), MP1.4 (GND), R10.2, R19.2, SW1.2 (B), SW5.G1, SW5.G2, U1.8 (GND), U1.9 (GND), U2.8 (GND), U2.9 (GND), U5.15 (VSS), U5.27 (VSSA), U5.31 (VSS), U5.47 (VSS), U5.63 (VSS), U6.2 (GND), U6.4 (GND), U6.5 (GND), U6.12 (SDO/ADDR), U8.4, U8.5 (GND), U8.6 (GND), U9.4, U9.5 (GND), U9.6 (GND), U10.2, U10.7 (GND), U10.8 (GND), U11.2, U11.7 (GND), U11.8 (GND), U12.2, U12.7 (GND), U12.8 (GND), U13.2, U13.7 (GND), U13.8 (GND), U14.2, U14.7 (GND), U14.8 (GND), U15.2, U15.7 (GND), U15.8 (GND)
Moteur_1_FWD: TP6.1, U1.4 (FWD), U5.8 (PC0)
Moteur_1_OUT+: C69.2, J1.6, U1.1 (OUT1)
Moteur_1_OUT-: C70.1, J1.1, U1.7 (OUT2)
Moteur_1_REV: TP8.1, U1.5 (REV), U5.2 (PC13)
Moteur_2_FWD: TP3.1, U2.4 (FWD), U5.51 (PA15)
Moteur_2_OUT+: C71.2, J2.6, U2.1 (OUT1)
Moteur_2_OUT-: C72.1, J2.1, U2.7 (OUT2)
Moteur_2_REV: TP4.1, U2.5 (REV), U5.56 (PB3)
NRST: C26.1, J10.12 (~RST), SW1.1 (A), U5.7 (PG10)
unnamed: C37.1, R17.2
unnamed: C38.1, R18.1, R19.1, R20.1
unnamed: D3.2 (A), R12.2
unnamed: D4.2 (A), R13.2
unnamed: D5.2 (A), R14.2
unnamed: J9.2, SW5.2
unnamed: MP1.5 (BST), R17.1
unnamed: MP1.6 (EN/SYNC), R15.2
unnamed: MP1.8 (FB), R18.2
unnamed: C37.2, L2.1, MP1.3 (SW)
unnamed: C35.1, MP1.7 (VCC), R16.1
PG: MP1.1 (PG), R16.2, U5.34 (PB12)
PWM_LED: J4.2, U5.36 (PB14)
PWM_LIDAR_MCTR: J5.1, U5.41 (PC9)
SWCLK: J10.6 (JCLK/SWCLK), U5.50 (PA14)
SWDIO: J10.4 (JTMS/SWDIO), U5.49 (PA13)
TOF_1_GPIO: U5.26 (PB2), U12.5
TOF_1_XSHUT: U5.33 (PB11), U12.6
TOF_2_GPIO: U5.25 (PB1), U11.5
TOF_2_XSHUT: U5.30 (PB10), U11.6
TOF_3_GPIO: U5.24 (PB0), U10.5
TOF_3_XSHUT: U5.20 (PA6), U10.6
TOF_4_GPIO: U5.22 (PC4), U13.5
TOF_4_XSHUT: U5.19 (PA5), U13.6
TOF_5_GPIO: U5.23 (PC5), U14.5
TOF_5_XSHUT: U5.18 (PA4), U14.6
TOF_6_GPIO: U5.21 (PA7), U15.5
TOF_6_XSHUT: U5.17 (PA3), U15.6
TOF_SCL: R22.2, U5.38 (PC6), U10.3, U11.3, U12.3, U13.3, U14.3, U15.3
TOF_SDA: R21.2, U5.39 (PC7), U10.4, U11.4, U12.4, U13.4, U14.4, U15.4
UART_Debug_RX: J10.13 (VCP_RX), U5.53 (PC11)
UART_Debug_TX: J10.14 (VCP_TX), U5.52 (PC10)
UART_LIDAR_TX_HD: J5.3, U5.59 (PB6)
UART_mp3_RX: U5.55 (PD2), U9.2
UART_mp3_TX: U5.54 (PC12), U9.1

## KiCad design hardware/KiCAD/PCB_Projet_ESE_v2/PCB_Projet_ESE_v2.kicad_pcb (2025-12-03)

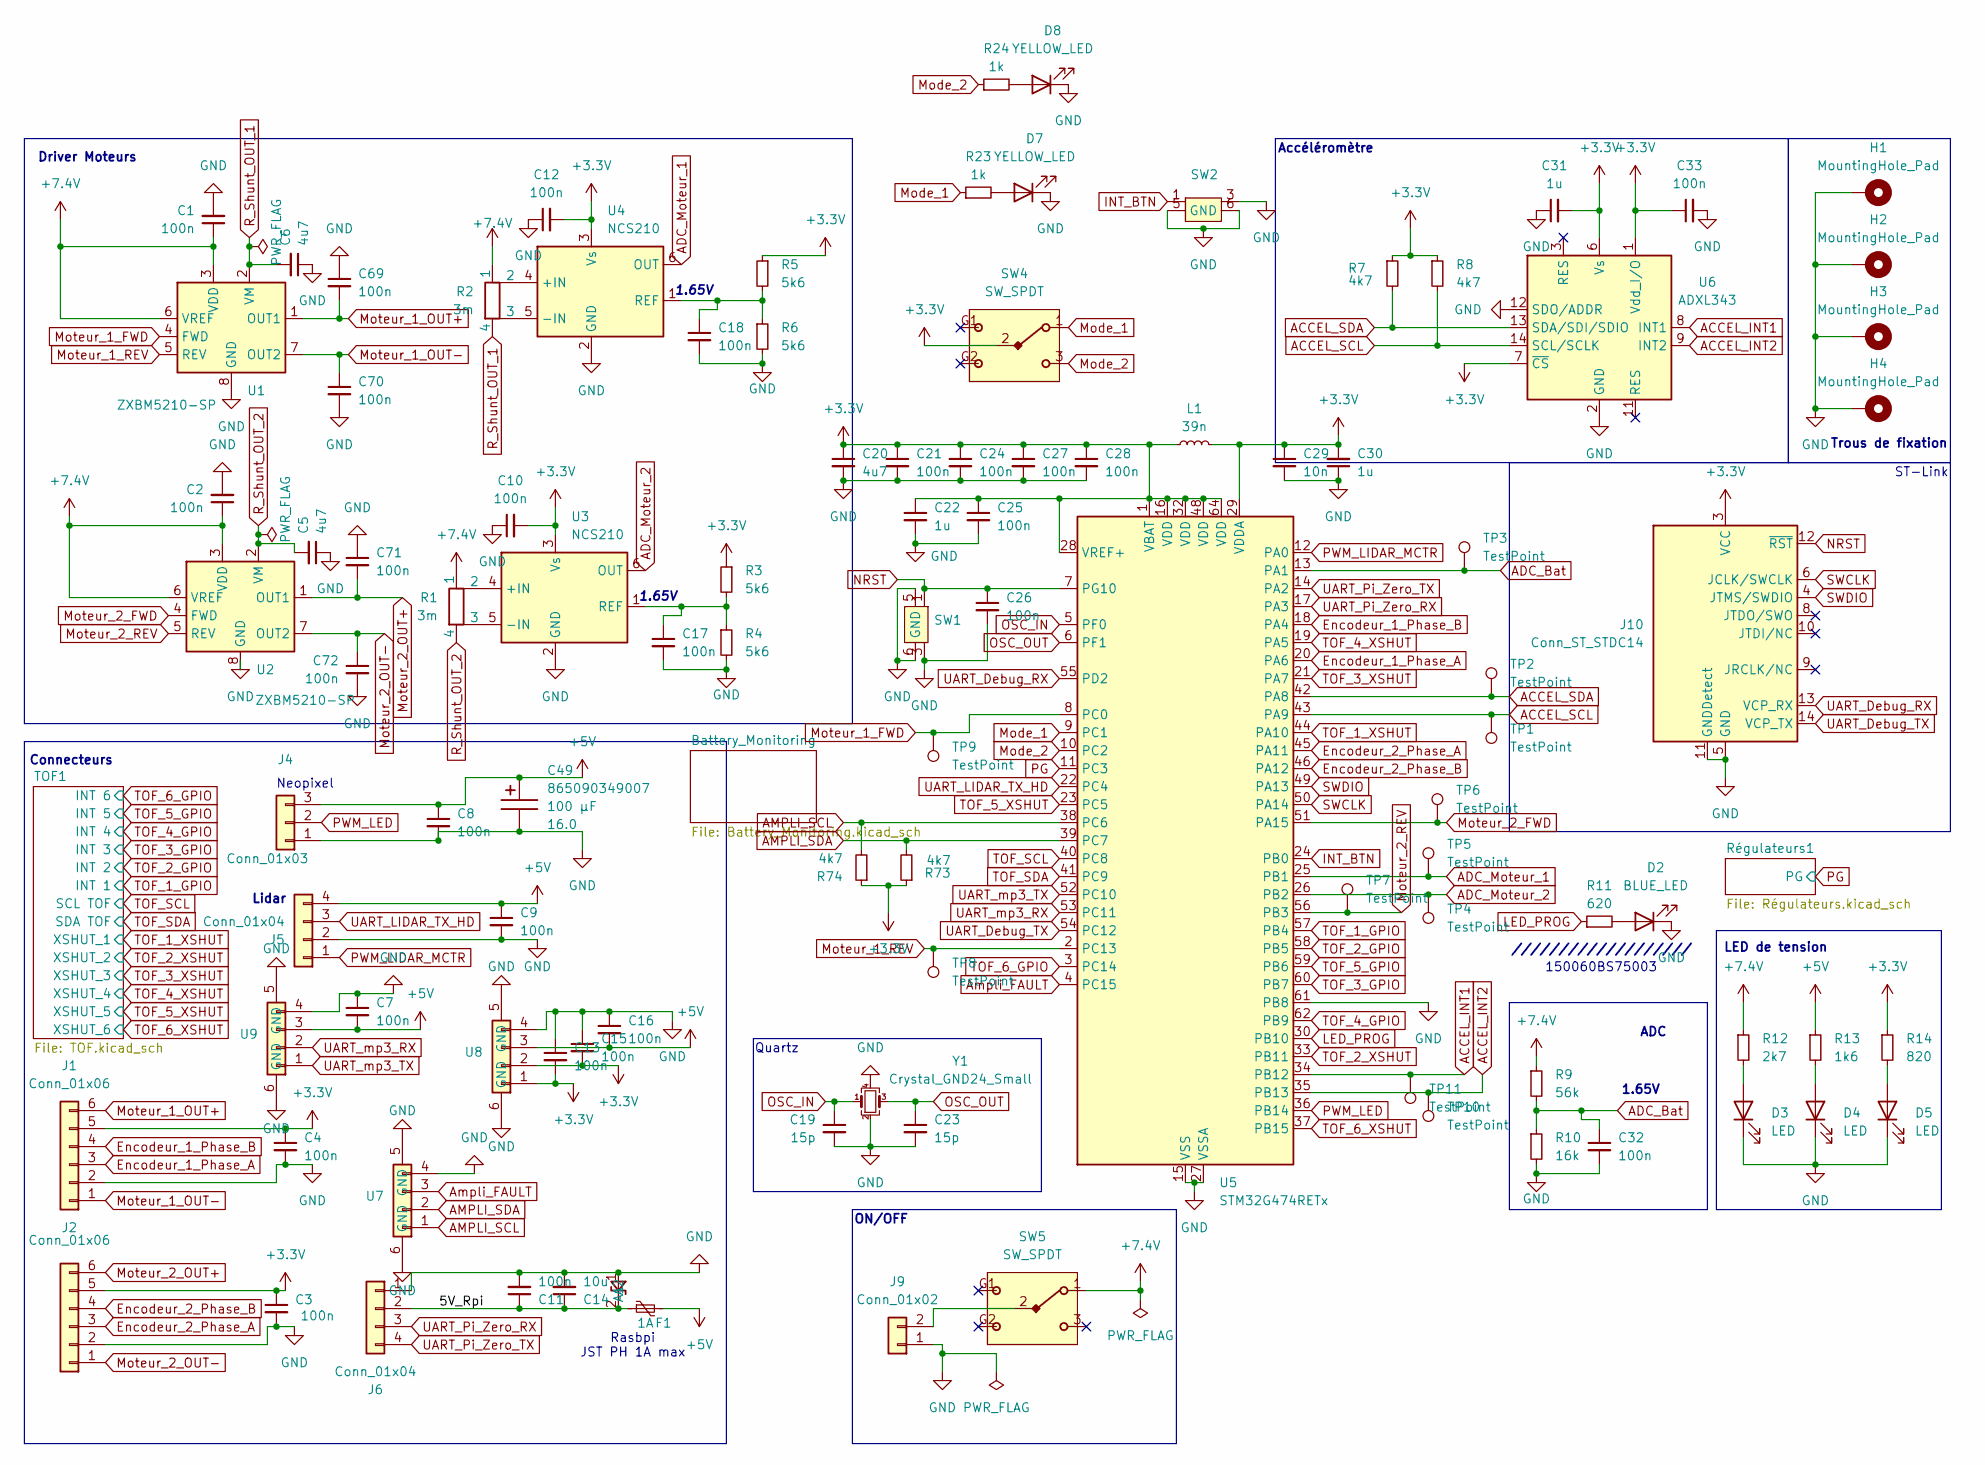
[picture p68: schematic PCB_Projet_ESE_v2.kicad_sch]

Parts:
C1, C2, C3, C4, C7, C8, C9, C10, C11, C12, C13, C15, C16, C17, C18, C21, C24, C25, C26, C27, C28, C32, C33, C69, C70, C71, C72: 100n; C_0402_1005Metric
C5, C6, C20: 4u7; C_0603_1608Metric
C14: 10u; C_0603_1608Metric
C19, C23: 15p; C_0603_1608Metric
C22, C30, C31: 1u; C_0402_1005Metric
C29: 10n; C_0402_1005Metric
C49: D8L6.5_865090349007; CP_Wurth_WCAP-ASLU-D8L6.5; Voltage 16.0; Part Number 865090349007
D2: BLUE_LED; LED_0603_1608Metric; MPN VLMB1501-GS08
D3, D4, D5: LED; LED_0603_1608Metric
D7, D8: YELLOW_LED; wurth_155060YS75300; MPN 155060YS75300
D20: D_SOD-523
F1: 1A; Fuse_2920_7451Metric; MPN 0ZAF0013FF28
H1, H2, H3, H4: MountingHole_Pad; Pad_traversant_M1
J1, J2: Conn_01x06; JST_PH_S6B-PH-K_1x06_P2.00mm_Horizontal
J4: Conn_01x03; JST_PH_B3B-PH-K_1x03_P2.00mm_Vertical
J5, J6: Conn_01x04; J_Wurth_WR-WTB_62000411722
J9: Conn_01x02; AMASS_XT30U-M_1x02_P5.0mm_Vertical
J10: Conn_ST_STDC14; PinHeader_2x07_P1.27mm_Vertical_SMD; MPN STLINK-V3MINIE
L1: 39n; L_0603_1608Metric
R1, R2: 3m; R_Shunt_Vishay_WSK2512_6332Metric_T2.21mm; MPN WSK25123L000DEA
R3, R4, R5, R6: 5k6; R_0402_1005Metric
R7, R8, R73, R74: 4k7; R_0402_1005Metric
R9: 56k; R_0402_1005Metric
R10: 16k; R_0402_1005Metric
R11: 620; R_0402_1005Metric
R12: 2k7; R_0402_1005Metric
R13: 1k6; R_0402_1005Metric
R14: 820; R_0402_1005Metric
R23, R24: 1k; R_0402_1005Metric
SW1, SW2: WS-TASV SMT Tact Switch 3.0 x 2.6 mm
SW4, SW5: SW_SPDT; SW_Wurth_WS-TOTV_472123020421; Part Number 472121010111
TP1, TP2, TP3, TP4, TP5, TP6, TP7, TP8, TP9, TP10, TP11: TestPoint; TestPoint_Pad_D1.0mm
U1, U2: ZXBM5210-SP; Diodes_SO-8EP; MPN ZXBM5210-SP-13
U3, U4: NCS210; SOT-363_SC-70-6
U5: STM32G474RETx; LQFP-64_10x10mm_P0.5mm
U6: ADXL343; LGA-14_3x5mm_P0.8mm_LayoutBorder1x6y; MPN ADXL343BCCZ-RL
U7, U8, U9: Wurth_Vertical_4_pos_0.8mm
Y1: Crystal_GND24_Small; Crystal_SMD_3225-4Pin_3.2x2.5mm; MPN Farnell : 2853935

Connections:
+3.3V: C3.1, C4.1, C10.2, C12.2, C13.2, C15.2, C20.1, C21.1, C22.1, C24.1, C25.1, C27.1, C28.1, C29.1, C30.2, C31.2, C33.1, J1.5, J2.5, J10.3 (VCC), L1.1, L1.2, R3.1, R5.1, R7.1, R8.1, R14.1, R73.1, R74.1, SW4.2, U3.3 (Vs), U4.3 (Vs), U5.1 (VBAT), U5.16 (VDD), U5.28 (VREF+), U5.29 (VDDA), U5.32 (VDD), U5.48 (VDD), U5.64 (VDD), U6.1 (Vdd_I/O), U6.6 (Vs), U6.7 (~CS), U8.1, U8.2; also elsewhere on the board
+5V: C7.2, C8.1, C9.1, C16.2, C49.1, F1.2, J4.3, J5.4, R13.1, U8.3, U9.3; also elsewhere on the board
+7.4V: C1.1, C2.1, R1.1, R2.1, R9.1, R12.1, SW5.1, U1.3 (VDD), U1.6 (VREF), U2.3 (VDD), U2.6 (VREF); also elsewhere on the board
/5V_Rpi: C11.1, C14.1, D20.2 (A2), F1.1, J6.2
ACCEL_INT1: TP11.1, U5.34 (PB12), U6.8 (INT1)
ACCEL_INT2: TP10.1, U5.35 (PB13), U6.9 (INT2)
ACCEL_SCL: R8.2, TP1.1, U5.43 (PA9), U6.14 (SCL/SCLK)
ACCEL_SDA: R7.2, TP2.1, U5.42 (PA8), U6.13 (SDA/SDI/SDIO)
ADC_Bat: C32.1, R9.2, R10.1, TP3.1, U5.13 (PA1)
ADC_Moteur_1: TP5.1, U4.6 (OUT), U5.25 (PB1)
ADC_Moteur_2: TP4.1, U3.6 (OUT), U5.26 (PB2)
AMPLI_SCL: R74.2, U5.38 (PC6), U7.1
AMPLI_SDA: R73.2, U5.39 (PC7), U7.2
Ampli_FAULT: U5.4 (PC15), U7.3
Encodeur_1_Phase_A: J1.3, U5.20 (PA6)
Encodeur_1_Phase_B: J1.4, U5.18 (PA4)
Encodeur_2_Phase_A: J2.3, U5.45 (PA11)
Encodeur_2_Phase_B: J2.4, U5.46 (PA12)
GND: C1.2, C2.2, C3.2, C4.2, C5.1, C6.1, C7.1, C8.2, C9.2, C10.1, C11.2, C12.1, C13.1, C14.2, C15.1, C16.1, C17.2, C18.2, C19.2, C20.2, C21.2, C22.2, C23.2, C24.2, C25.2, C26.2, C27.2, C28.2, C29.2, C30.1, C31.1, C32.2, C33.2, C49.2, C69.1, C70.2, C71.1, C72.2, D2.1 (K), D3.1 (K), D4.1 (K), D5.1 (K), D7.1 (K), D8.1 (K), D20.1 (A1), H1.1, H2.1, H3.1, H4.1, J1.2, J2.2, J4.1, J5.2, J6.1, J9.1, J10.5 (GND), J10.7 (GND), J10.11 (GNDDetect), R4.2, R6.2, R10.2, SW1.3, SW1.4, SW1.5, SW1.6 (GND), SW2.3, SW2.4, SW2.5, SW2.6 (GND), U1.8 (GND), U1.9 (GND), U2.8 (GND), U2.9 (GND), U3.2 (GND), U4.2 (GND), U5.15 (VSS), U5.27 (VSSA), U5.31 (VSS), U5.47 (VSS), U5.61 (PB8), U5.63 (VSS), U6.2 (GND), U6.4 (GND), U6.5 (GND), U6.12 (SDO/ADDR), U7.4, U7.5 (GND), U7.6 (GND), U8.4, U8.5 (GND), U8.6 (GND), U9.4, U9.5 (GND), U9.6 (GND), Y1.2, Y1.4; also elsewhere on the board
INT_BTN: SW2.1, SW2.2, U5.24 (PB0)
LED_PROG: R11.1, U5.30 (PB10)
Mode_1: R23.1, SW4.1, U5.9 (PC1)
Mode_2: R24.1, SW4.3, U5.10 (PC2)
Moteur_1_FWD: TP9.1, U1.4 (FWD), U5.8 (PC0)
Moteur_1_OUT+: C69.2, J1.6, U1.1 (OUT1)
Moteur_1_OUT-: C70.1, J1.1, U1.7 (OUT2)
Moteur_1_REV: TP8.1, U1.5 (REV), U5.2 (PC13)
Moteur_2_FWD: TP6.1, U2.4 (FWD), U5.51 (PA15)
Moteur_2_OUT+: C71.2, J2.6, U2.1 (OUT1)
Moteur_2_OUT-: C72.1, J2.1, U2.7 (OUT2)
Moteur_2_REV: TP7.1, U2.5 (REV), U5.56 (PB3)
NRST: C26.1, J10.12 (~RST), SW1.1, SW1.2, U5.7 (PG10)
unnamed: D2.2 (A), R11.2
unnamed: D3.2 (A), R12.2
unnamed: D4.2 (A), R13.2
unnamed: D5.2 (A), R14.2
unnamed: D7.2 (A), R23.2
unnamed: D8.2 (A), R24.2
unnamed: J9.2, SW5.2
unnamed: R1.2, U3.4 (+IN)
unnamed: R1.3, U3.5 (-IN)
unnamed: C17.1, R3.2, R4.1, U3.1 (REF)
unnamed: R2.2, U4.4 (+IN)
unnamed: R2.3, U4.5 (-IN)
unnamed: C18.1, R5.2, R6.1, U4.1 (REF)
OSC_IN: C19.1, U5.5 (PF0), Y1.1
OSC_OUT: C23.1, U5.6 (PF1), Y1.3
PG: U5.11 (PC3); also elsewhere on the board
PWM_LED: J4.2, U5.36 (PB14)
PWM_LIDAR_MCTR: J5.1, U5.12 (PA0)
R_Shunt_OUT_1: C6.2, R2.4, U1.2 (VM)
R_Shunt_OUT_2: C5.2, R1.4, U2.2 (VM)
SWCLK: J10.6 (JCLK/SWCLK), U5.50 (PA14)
SWDIO: J10.4 (JTMS/SWDIO), U5.49 (PA13)
TOF_1_GPIO: U5.57 (PB4); also elsewhere on the board
TOF_1_XSHUT: U5.44 (PA10); also elsewhere on the board
TOF_2_GPIO: U5.58 (PB5); also elsewhere on the board
TOF_2_XSHUT: U5.33 (PB11); also elsewhere on the board
TOF_3_GPIO: U5.60 (PB7); also elsewhere on the board
TOF_3_XSHUT: U5.21 (PA7); also elsewhere on the board
TOF_4_GPIO: U5.62 (PB9); also elsewhere on the board
TOF_4_XSHUT: U5.19 (PA5); also elsewhere on the board
TOF_5_GPIO: U5.59 (PB6); also elsewhere on the board
TOF_5_XSHUT: U5.23 (PC5); also elsewhere on the board
TOF_6_GPIO: U5.3 (PC14); also elsewhere on the board
TOF_6_XSHUT: U5.37 (PB15); also elsewhere on the board
TOF_SCL: U5.40 (PC8); also elsewhere on the board
TOF_SDA: U5.41 (PC9); also elsewhere on the board
UART_Debug_RX: J10.13 (VCP_RX), U5.55 (PD2)
UART_Debug_TX: J10.14 (VCP_TX), U5.54 (PC12)
UART_LIDAR_TX_HD: J5.3, U5.22 (PC4)
UART_Pi_Zero_RX: J6.3, U5.17 (PA3)
UART_Pi_Zero_TX: J6.4, U5.14 (PA2)
UART_mp3_RX: U5.53 (PC11), U9.2
UART_mp3_TX: U5.52 (PC10), U9.1

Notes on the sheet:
Rasbpi JST PH 1A max
ST-Link
ON/OFF
LED de tension
Driver Moteurs
Lidar
Connecteurs
Neopixel
Accéléromètre
Quartz
ADC
///////////////////
1.65V
Trous de fixation
150060BS75003

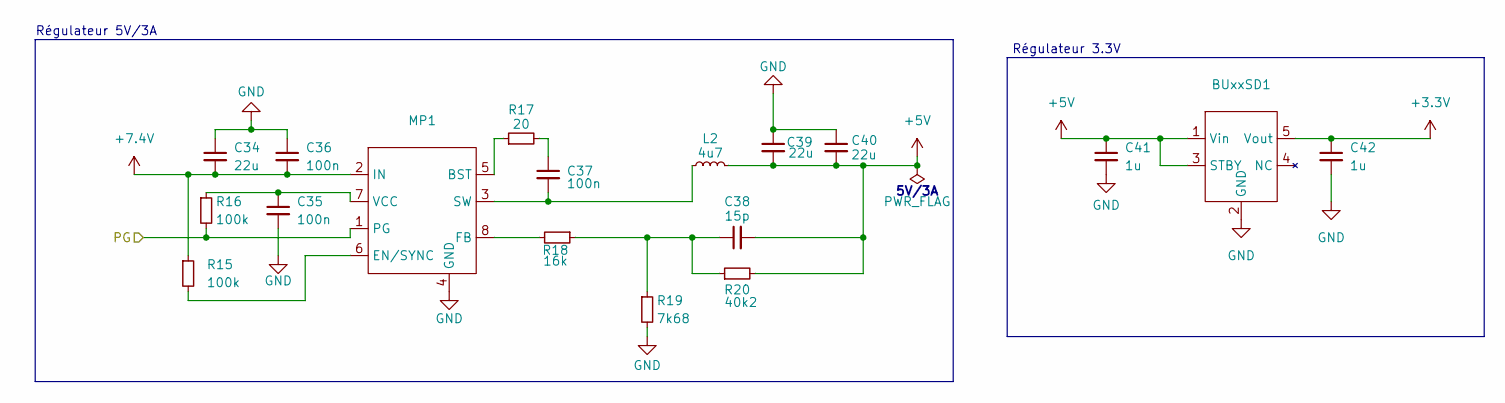
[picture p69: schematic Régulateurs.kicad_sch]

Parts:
BUxxSD1: SSOP5_BUxxSD5; MPN BU33SD5WG-TR
C34: 22u; C_1206_3216Metric
C35, C36, C37: 100n; C_0402_1005Metric
C38: 15p; C_0402_1005Metric
C39, C40: 22u; C_0805_2012Metric
C41, C42: 1u; C_0402_1005Metric
L2: 4u7; 74404054068
MP1: TSOT23-8; MPN MP1475DJ-LF-P
R15, R16: 100k; R_0402_1005Metric
R17: 20; R_0402_1005Metric
R18: 16k; R_0402_1005Metric
R19: 7k68; R_0402_1005Metric
R20: 40k2; R_0402_1005Metric

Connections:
+3.3V: BUxxSD1.5 (Vout), C42.1; also elsewhere on the board
+5V: BUxxSD1.1 (Vin), BUxxSD1.3 (STBY), C38.2, C39.2, C40.2, C41.1, L2.2, R20.2; also elsewhere on the board
+7.4V: C34.2, C36.2, MP1.2 (IN), R15.1; also elsewhere on the board
GND: BUxxSD1.2 (GND), C34.1, C35.2, C36.1, C39.1, C40.1, C41.2, C42.2, MP1.4 (GND), R19.2; also elsewhere on the board
unnamed: C37.1, R17.2
unnamed: C38.1, R18.1, R19.1, R20.1
unnamed: MP1.5 (BST), R17.1
unnamed: MP1.6 (EN/SYNC), R15.2
unnamed: MP1.8 (FB), R18.2
unnamed: C37.2, L2.1, MP1.3 (SW)
unnamed: C35.1, MP1.7 (VCC), R16.1
PG: MP1.1 (PG), R16.2; also elsewhere on the board

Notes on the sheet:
Régulateur 3.3V
5V/3A
Régulateur 5V/3A

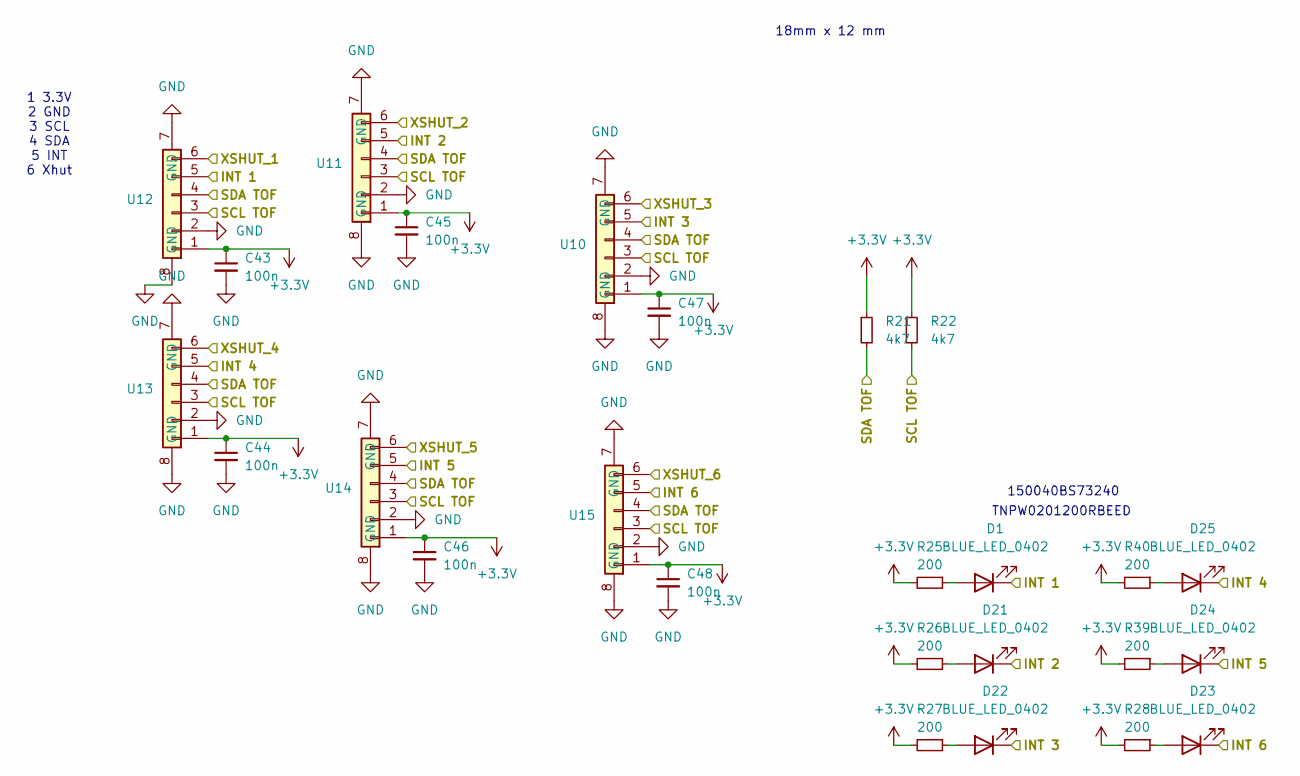
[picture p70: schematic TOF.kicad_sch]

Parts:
C43, C44, C45, C46, C47, C48: 100n; C_0402_1005Metric
D1, D21, D22, D23, D24, D25: BLUE_LED_0402; LED_0402_1005Metric
R21, R22: 4k7; R_0402_1005Metric
R25, R26, R27, R28, R39, R40: 200; R_0201_0603Metric
U10, U11, U12, U13, U14, U15: Wurth_Vertical_6_pos_0.8mm

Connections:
+3.3V: C43.1, C44.1, C45.1, C46.1, C47.1, C48.1, R21.1, R22.1, R25.2, R26.2, R27.2, R28.2, R39.2, R40.2, U10.1, U11.1, U12.1, U13.1, U14.1, U15.1; also elsewhere on the board
GND: C43.2, C44.2, C45.2, C46.2, C47.2, C48.2, U10.2, U10.7 (GND), U10.8 (GND), U11.2, U11.7 (GND), U11.8 (GND), U12.2, U12.7 (GND), U12.8 (GND), U13.2, U13.7 (GND), U13.8 (GND), U14.2, U14.7 (GND), U14.8 (GND), U15.2, U15.7 (GND), U15.8 (GND); also elsewhere on the board
unnamed: D1.2 (A), R25.1
unnamed: D21.2 (A), R26.1
unnamed: D22.2 (A), R27.1
unnamed: D23.2 (A), R28.1
unnamed: D24.2 (A), R39.1
unnamed: D25.2 (A), R40.1
TOF_1_GPIO: D1.1 (K), U12.5; also elsewhere on the board
TOF_1_XSHUT: U12.6; also elsewhere on the board
TOF_2_GPIO: D21.1 (K), U11.5; also elsewhere on the board
TOF_2_XSHUT: U11.6; also elsewhere on the board
TOF_3_GPIO: D22.1 (K), U10.5; also elsewhere on the board
TOF_3_XSHUT: U10.6; also elsewhere on the board
TOF_4_GPIO: D25.1 (K), U13.5; also elsewhere on the board
TOF_4_XSHUT: U13.6; also elsewhere on the board
TOF_5_GPIO: D24.1 (K), U14.5; also elsewhere on the board
TOF_5_XSHUT: U14.6; also elsewhere on the board
TOF_6_GPIO: D23.1 (K), U15.5; also elsewhere on the board
TOF_6_XSHUT: U15.6; also elsewhere on the board
TOF_SCL: R22.2, U10.3, U11.3, U12.3, U13.3, U14.3, U15.3; also elsewhere on the board
TOF_SDA: R21.2, U10.4, U11.4, U12.4, U13.4, U14.4, U15.4; also elsewhere on the board

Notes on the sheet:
18mm x 12 mm
150040BS73240
TNPW0201200RBEED
1 3.3V 2 GND 3 SCL 4 SDA 5 INT 6 Xhut

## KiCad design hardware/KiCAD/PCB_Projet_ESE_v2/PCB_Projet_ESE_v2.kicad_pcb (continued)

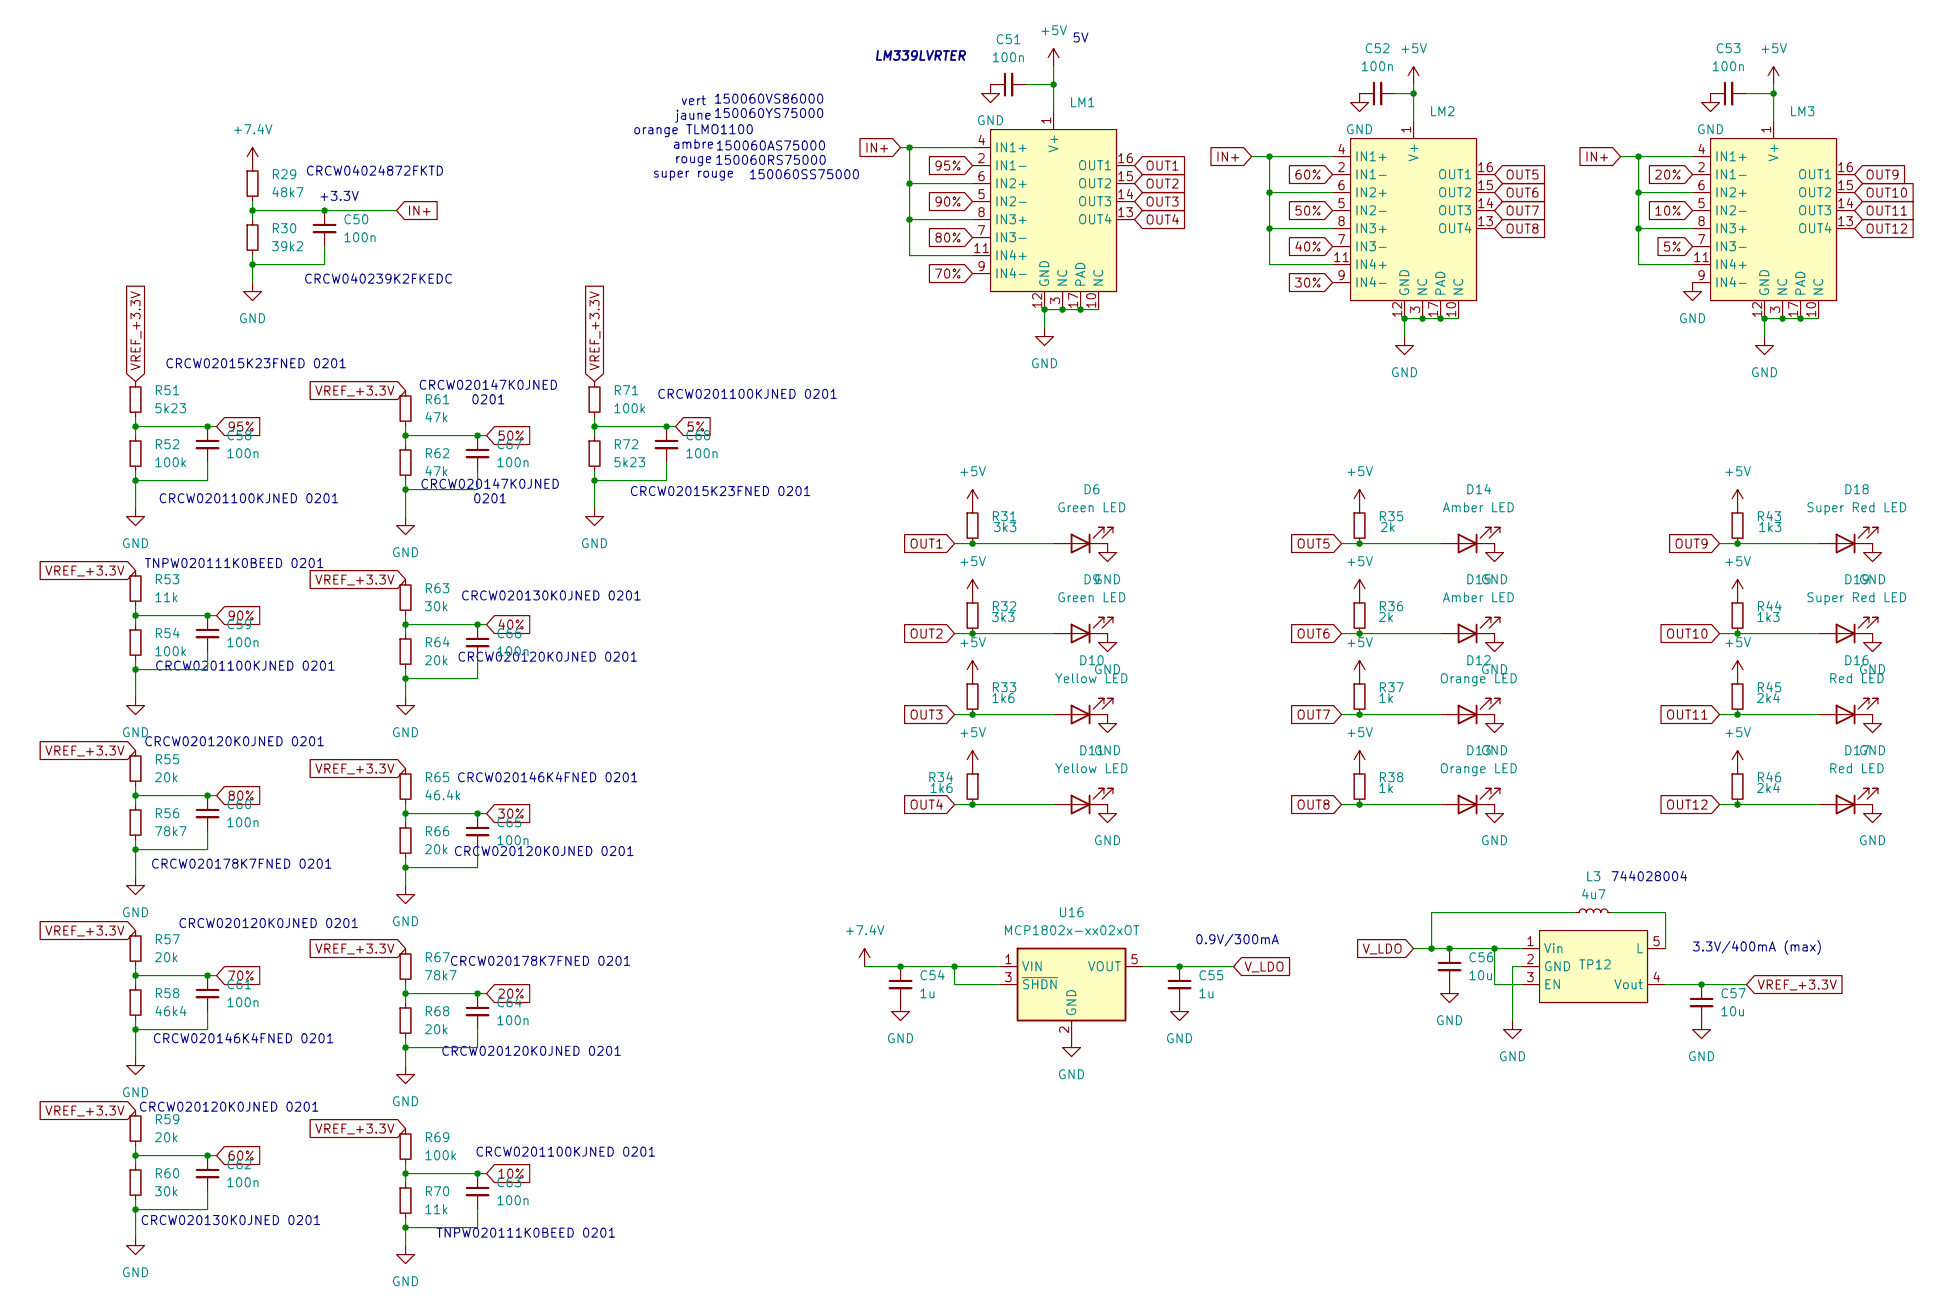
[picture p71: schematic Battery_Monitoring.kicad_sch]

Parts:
C50, C51, C52, C53, C58, C59, C60, C61, C62, C63, C64, C65, C66, C67, C68: 100n; C_0402_1005Metric
C54, C55: 1u; C_0402_1005Metric
C56, C57: 10u; C_0603_1608Metric
D6, D9: Green LED; LED_0603_1608Metric
D10, D11: Yellow LED; LED_0603_1608Metric
D12, D13: Orange LED; LED_0603_1608Metric
D14, D15: Amber LED; LED_0603_1608Metric
D16, D17: Red LED; LED_0603_1608Metric
D18, D19: Super Red LED; LED_0603_1608Metric
L3: 4u7; WE-TPC-744028004
LM1: WQFN-16-1EP_3x3mm_P0.5mm_EP1.68x1.68mm
LM2, LM3: WQFN-16-1EP_3x3mm_P0.5mm_EP1.68x1.68mm; MPN LM339LVRTER
R29: 48k7; R_0402_1005Metric
R30: 39k2; R_0402_1005Metric
R31, R32: 3k3; R_0402_1005Metric
R33, R34: 1k6; R_0402_1005Metric
R35, R36: 2k; R_0402_1005Metric
R37, R38: 1k; R_0402_1005Metric
R43, R44: 1k3; R_0402_1005Metric
R45, R46: 2k4; R_0402_1005Metric
R51: 5k23; R_0201_0603Metric
R52, R54, R69, R71: 100k; R_0201_0603Metric
R53, R70: 11k; R_0201_0603Metric
R55, R57, R59, R64, R66, R68: 20k; R_0201_0603Metric
R56, R67: 78k7; R_0201_0603Metric
R58: 46k4; R_0201_0603Metric
R60, R63: 30k; R_0201_0603Metric
R61, R62: 47k; R_0201_0603Metric
R65: 46.4k; R_0201_0603Metric
R72: 5k23; R_0402_1005Metric
TP12: SOT-23-5; MPN TPS61097A-33DBVR
U16: MCP1802x-xx02xOT; SOT-23-5; MPN MCP1802T-0902I/OT

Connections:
5%: C68.1, LM3.7 (IN3-), R71.2, R72.1
10%: C63.1, LM3.5 (IN2-), R69.2, R70.1
20%: C64.1, LM3.2 (IN1-), R67.2, R68.1
30%: C65.1, LM2.9 (IN4-), R65.2, R66.1
40%: C66.1, LM2.7 (IN3-), R63.2, R64.1
50%: C67.1, LM2.5 (IN2-), R61.2, R62.1
60%: C62.1, LM2.2 (IN1-), R59.2, R60.1
70%: C61.1, LM1.9 (IN4-), R57.2, R58.1
80%: C60.1, LM1.7 (IN3-), R55.2, R56.1
90%: C59.1, LM1.5 (IN2-), R53.2, R54.1
95%: C58.1, LM1.2 (IN1-), R51.2, R52.1
+5V: C51.2, C52.2, C53.2, LM1.1 (V+), LM2.1 (V+), LM3.1 (V+), R31.1, R32.1, R33.1, R34.1, R35.1, R36.1, R37.1, R38.1, R43.1, R44.1, R45.1, R46.1; also elsewhere on the board
+7.4V: C54.1, R29.1, U16.1 (VIN), U16.3 (~SHDN); also elsewhere on the board
GND: C50.2, C51.1, C52.1, C53.1, C54.2, C55.2, C56.2, C57.2, C58.2, C59.2, C60.2, C61.2, C62.2, C63.2, C64.2, C65.2, C66.2, C67.2, C68.2, D6.1 (K), D9.1 (K), D10.1 (K), D11.1 (K), D12.1 (K), D13.1 (K), D14.1 (K), D15.1 (K), D16.1 (K), D17.1 (K), D18.1 (K), D19.1 (K), LM1.3 (NC), LM1.10 (NC), LM1.12 (GND), LM1.17 (PAD), LM2.3 (NC), LM2.10 (NC), LM2.12 (GND), LM2.17 (PAD), LM3.3 (NC), LM3.9 (IN4-), LM3.10 (NC), LM3.12 (GND), LM3.17 (PAD), R30.2, R52.2, R54.2, R56.2, R58.2, R60.2, R62.2, R64.2, R66.2, R68.2, R70.2, R72.2, TP12.2 (GND), U16.2 (GND); also elsewhere on the board
IN+: C50.1, LM1.4 (IN1+), LM1.6 (IN2+), LM1.8 (IN3+), LM1.11 (IN4+), LM2.4 (IN1+), LM2.6 (IN2+), LM2.8 (IN3+), LM2.11 (IN4+), LM3.4 (IN1+), LM3.6 (IN2+), LM3.8 (IN3+), LM3.11 (IN4+), R29.2, R30.1
unnamed: L3.2, TP12.5 (L)
OUT1: D6.2 (A), LM1.16 (OUT1), R31.2
OUT2: D9.2 (A), LM1.15 (OUT2), R32.2
OUT3: D10.2 (A), LM1.14 (OUT3), R33.2
OUT4: D11.2 (A), LM1.13 (OUT4), R34.2
OUT5: D14.2 (A), LM2.16 (OUT1), R35.2
OUT6: D15.2 (A), LM2.15 (OUT2), R36.2
OUT7: D12.2 (A), LM2.14 (OUT3), R37.2
OUT8: D13.2 (A), LM2.13 (OUT4), R38.2
OUT9: D18.2 (A), LM3.16 (OUT1), R43.2
OUT10: D19.2 (A), LM3.15 (OUT2), R44.2
OUT11: D16.2 (A), LM3.14 (OUT3), R45.2
OUT12: D17.2 (A), LM3.13 (OUT4), R46.2
VREF_+3.3V: C57.1, R51.1, R53.1, R55.1, R57.1, R59.1, R61.1, R63.1, R65.1, R67.1, R69.1, R71.1, TP12.4 (Vout)
V_LDO: C55.1, C56.1, L3.1, TP12.1 (Vin), TP12.3 (EN), U16.5 (VOUT)

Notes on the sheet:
CRCW020147K0JNED 0201
TNPW020111K0BEED 0201
CRCW0201100KJNED 0201
CRCW04024872FKTD
vert jaune orange TLMO1100 ambre rouge super rouge
150060YS75000
CRCW020146K4FNED 0201
CRCW020120K0JNED 0201
CRCW020178K7FNED 0201
744028004
CRCW020130K0JNED 0201
+3.3V
CRCW02015K23FNED 0201
3.3V/400mA (max)
150060VS86000
150060AS75000
150060RS75000
CRCW040239K2FKEDC
150060SS75000
LM339LVRTER
0.9V/300mA

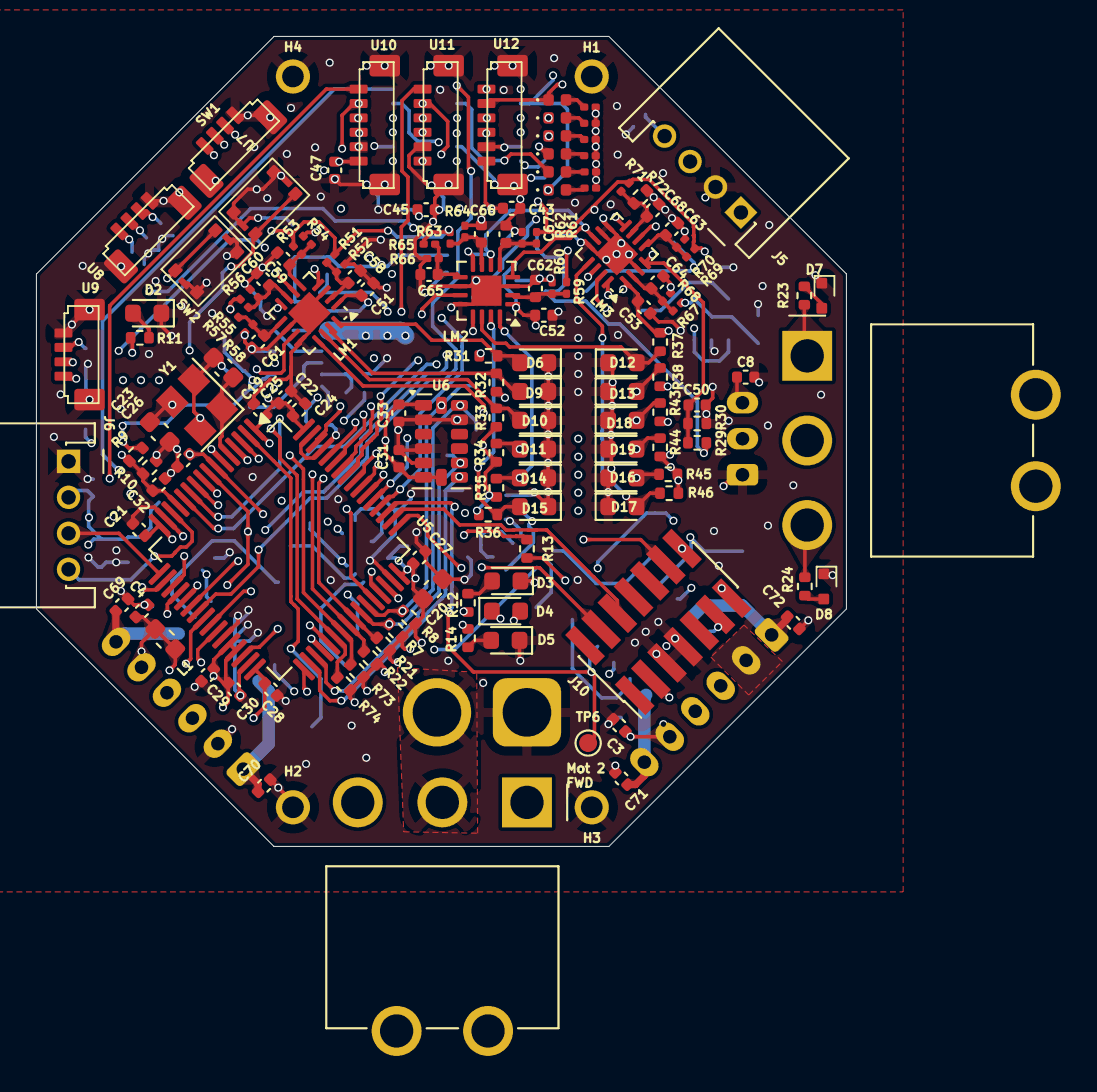
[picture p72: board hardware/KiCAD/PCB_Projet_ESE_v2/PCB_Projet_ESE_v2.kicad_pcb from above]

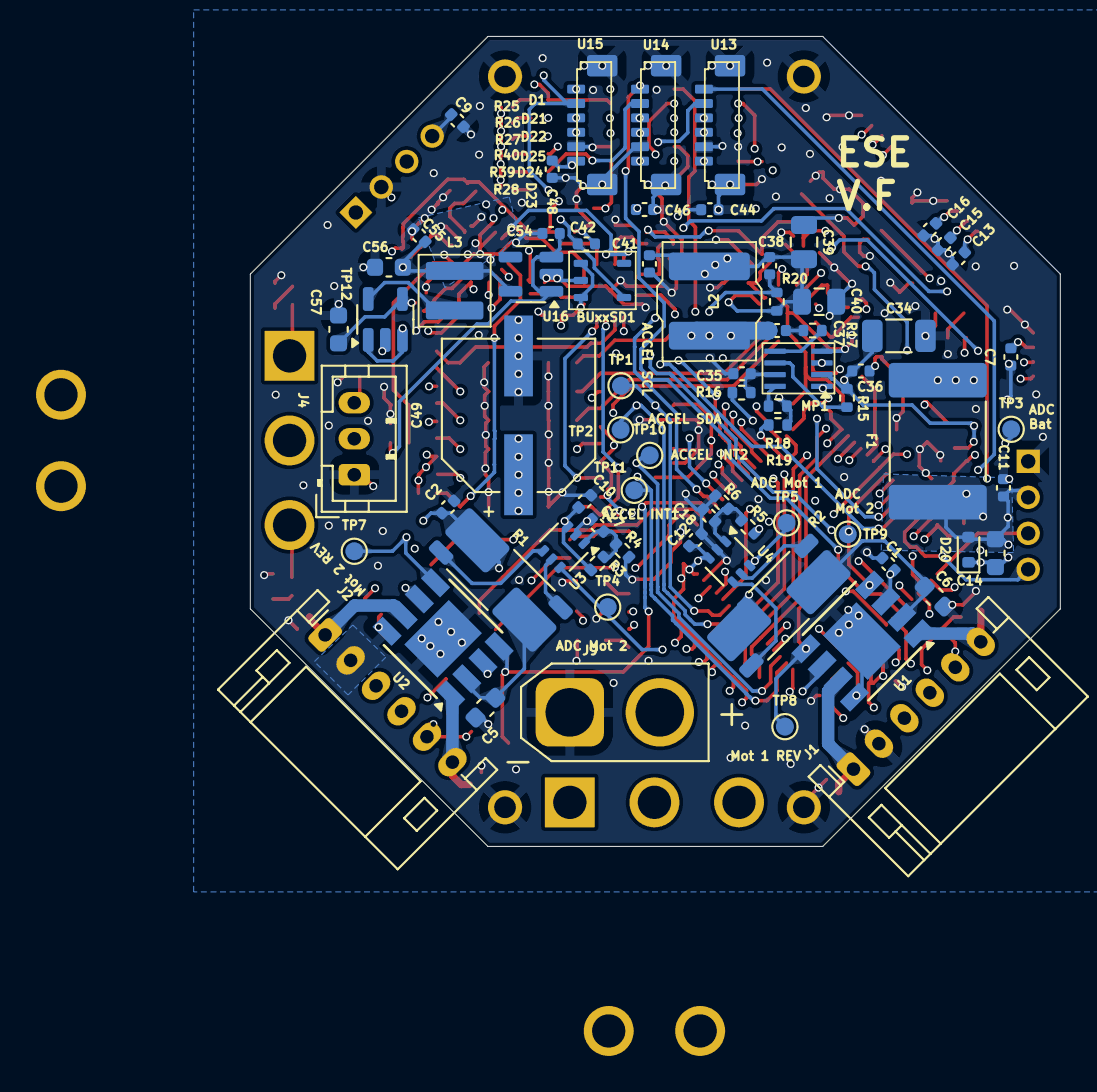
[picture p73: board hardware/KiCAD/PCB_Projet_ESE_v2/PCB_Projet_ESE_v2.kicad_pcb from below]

Board: 8 copper layers, 45.0 x 45.0 mm, 218 parts (73 on the bottom side), 115 nets.

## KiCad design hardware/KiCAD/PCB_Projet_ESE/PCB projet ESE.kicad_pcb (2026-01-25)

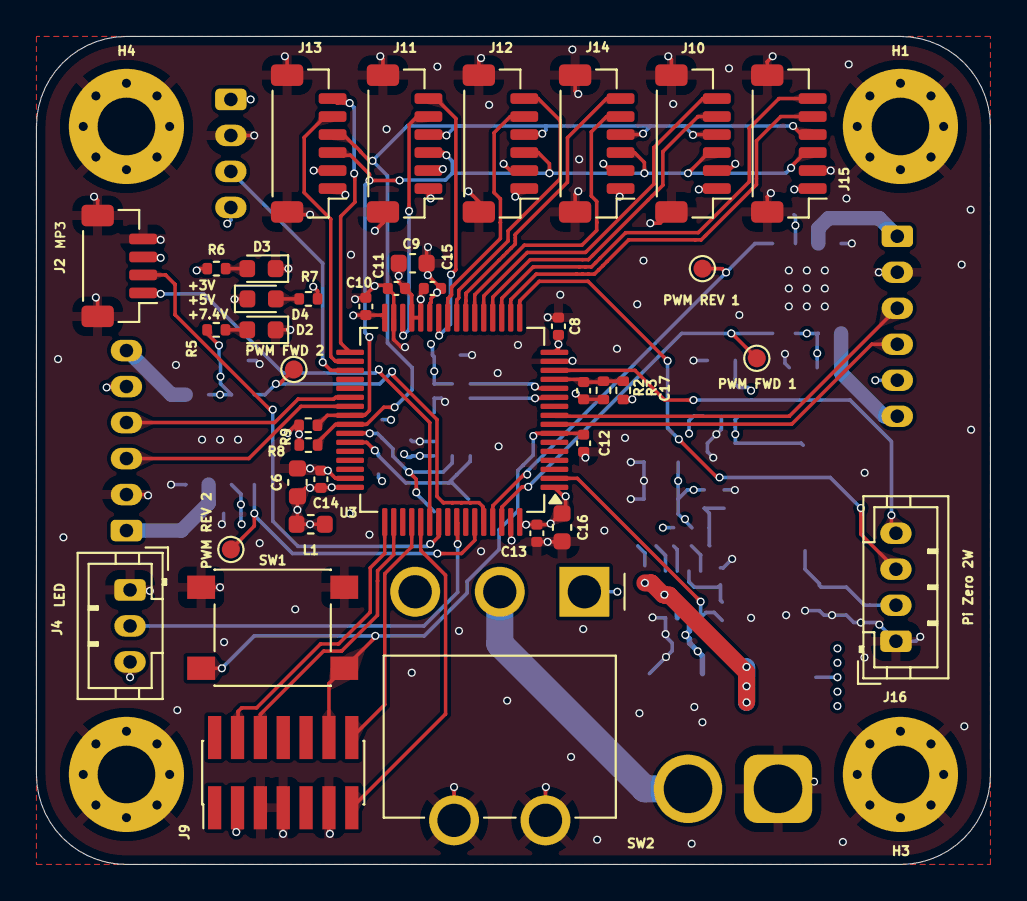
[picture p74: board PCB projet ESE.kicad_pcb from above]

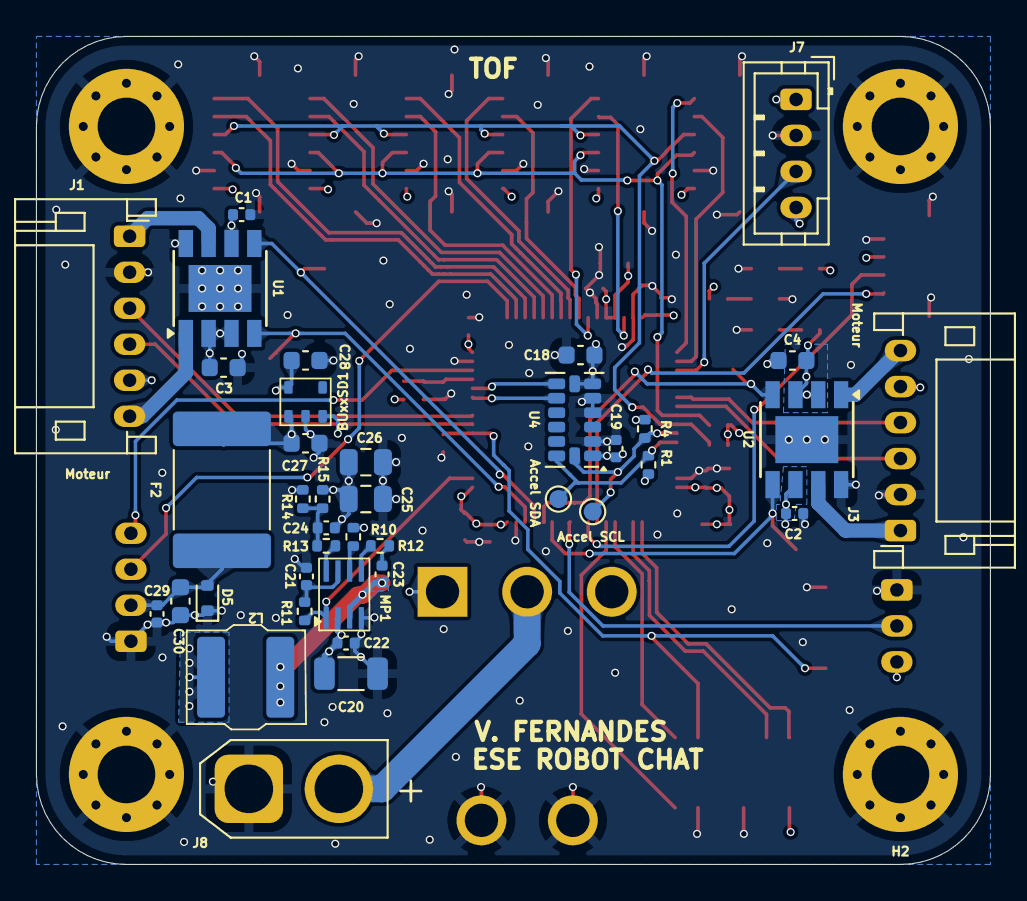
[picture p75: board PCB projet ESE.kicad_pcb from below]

Board: 4 copper layers, 53.0 x 46.0 mm, 82 parts (40 on the bottom side), 59 nets.

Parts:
Accel SCL: TestPoint; TestPoint_Pad_D1.0mm
Accel SDA: TestPoint; TestPoint_Pad_D1.0mm
BUxxSD1: SSOP5_BUxxSD5
C1, C2, C8, C10, C11, C12, C13, C14, C17, C19, C21, C22, C23, C29: 100n; C_0402_1005Metric
C3, C4, C6: 4u7; C_0603_1608Metric
C9, C16, C18, C27, C28: 1u; C_0603_1608Metric
C15: 10n; C_0402_1005Metric
C20: 22u; C_1206_3216Metric
C24: 15p; C_0402_1005Metric
C25, C26: 22u; C_0805_2012Metric
C30: 10u; C_0603_1608Metric
D2, D3, D4: LED; LED_0603_1608Metric
D5: D_TVS_Small; D_SOD-523
F2: 1A; Fuse_2920_7451Metric
H1, H2, H3, H4: MountingHole_Pad; MountingHole_3.2mm_M3_Pad_Via
J1, J3: Conn_01x06; JST_PH_S6B-PH-K_1x06_P2.00mm_Horizontal
J2: Conn_01x04; JST_SH_BM04B-SRSS-TB_1x04-1MP_P1.00mm_Vertical
J4: Conn_01x03; JST_PH_B3B-PH-K_1x03_P2.00mm_Vertical
J7, J16: Conn_01x04; JST_PH_B4B-PH-K_1x04_P2.00mm_Vertical
J8: Conn_01x02; AMASS_XT30U-M_1x02_P5.0mm_Vertical
J9: Conn_ST_STDC14; PinHeader_2x07_P1.27mm_Vertical_SMD
J10, J11, J12, J13, J14, J15: Conn_01x06; JST_SH_BM06B-SRSS-TB_1x06-1MP_P1.00mm_Vertical
L1: 39n; L_0603_1608Metric
L2: 4u7; 74404054068
MP1: TSOT23-8
PWM FWD 1, PWM FWD 2: TestPoint; TestPoint_Pad_D1.0mm
PWM REV 1, PWM REV 2: TestPoint; TestPoint_Pad_D1.0mm
R1, R4, R8, R9: 1k; R_0402_1005Metric
R2: 20k; R_0402_1005Metric
R3: 5k6; R_0402_1005Metric
R5: 2k9; R_0402_1005Metric
R6: 1k65; R_0402_1005Metric
R7: 800; R_0402_1005Metric
R10, R11: 100k; R_0402_1005Metric
R12: 20; R_0402_1005Metric
R13: 16k; R_0402_1005Metric
R14: 7k68; R_0402_1005Metric
R15: 40k2; R_0402_1005Metric
SW1: SW_SPST
SW2: 472121010111; SW_Wurth_WS-TOTV_472123020421
U1, U2: ZXBM5210-SP; Diodes_SO-8EP
U3: STM32G474RETx; LQFP-64_10x10mm_P0.5mm
U4: ADXL343; LGA-14_3x5mm_P0.8mm_LayoutBorder1x6y

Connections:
+3.3V: BUxxSD1.5 (Vout), C6.1, C8.1, C9.1, C10.1, C11.1, C13.1, C14.1, C15.1, C16.2, C18.2, C19.1, C28.1, J1.5, J3.5, J7.1, J9.3 (VCC), J10.1, J11.1, J12.1, J13.1, J14.1, J15.1, L1.1, L1.2, R1.1, R4.1, R7.1, R8.1, R9.1, U3.1 (VBAT), U3.16 (VDD), U3.28 (VREF+), U3.29 (VDDA), U3.32 (VDD), U3.48 (VDD), U3.64 (VDD), U4.1 (Vdd_I/O), U4.6 (Vs), U4.7 (~CS)
+5V: BUxxSD1.1 (Vin), BUxxSD1.3 (STBY), C24.2, C25.2, C26.2, C27.1, F2.2, J2.3, J4.3, J7.4, L2.2, R6.1, R15.2
+7.4V: C1.1, C2.1, C3.2, C4.2, C20.2, C22.2, MP1.2 (IN), R2.1, R5.1, R10.1, SW2.1, U1.2 (VM), U1.3 (VDD), U1.6 (VREF), U2.2 (VM), U2.3 (VDD), U2.6 (VREF)
/5V_Rpi: C29.1, C30.1, D5.2 (A2), F2.1, J16.2
ADC1_IN2: C17.1, R2.2, R3.1, U3.13 (PA1)
Accel SCL: Accel SCL.1, R4.2, U3.42 (PA8), U4.14 (SCL/SCLK)
Accel SDA: Accel SDA.1, R1.2, U3.43 (PA9), U4.13 (SDA/SDI/SDIO)
Encodeur_A_Phase_1: J1.3, U3.9 (PC1)
Encodeur_A_Phase_2: J3.3, U3.39 (PC7)
Encodeur_B_Phase_1: J1.4, U3.8 (PC0)
Encodeur_B_Phase_2: J3.4, U3.38 (PC6)
GND: BUxxSD1.2 (GND), C1.2, C2.2, C3.1, C4.1, C6.2, C8.2, C9.2, C10.2, C11.2, C12.2, C13.2, C14.2, C15.2, C16.1, C17.2, C18.1, C19.2, C20.1, C21.2, C22.1, C25.1, C26.1, C27.2, C28.2, C29.2, C30.2, D2.1 (K), D3.1 (K), D4.1 (K), D5.1 (A1), H1.1, H2.1, H3.1, H4.1, J1.2, J2.4, J2.MP, J3.2, J4.1, J7.2, J8.1, J9.5 (GND), J9.7 (GND), J9.11 (GNDDetect), J10.2, J10.MP, J11.2, J11.MP, J12.2, J12.MP, J13.2, J13.MP, J14.2, J14.MP, J15.2, J15.MP, J16.1, MP1.4 (GND), R3.2, R14.2, SW1.2 (B), SW2.G1, SW2.G2, U1.8 (GND), U1.9 (GND), U2.8 (GND), U2.9 (GND), U3.15 (VSS), U3.27 (VSSA), U3.31 (VSS), U3.47 (VSS), U3.63 (VSS), U4.2 (GND), U4.4 (GND), U4.5 (GND)
INT 1: U3.12 (PA0), U4.8 (INT1)
INT 2: U3.11 (PC3), U4.9 (INT2)
INT_1: J10.5, U3.20 (PA6)
INT_2: J12.5, U3.25 (PB1)
INT_3: J14.5, U3.22 (PC4)
INT_4: J11.5, U3.30 (PB10)
INT_5: J13.5, U3.34 (PB12)
INT_6: J15.5, U3.18 (PA4)
Lidar Output: J7.3, U3.35 (PB13)
Moteur + 1: J1.6, U1.1 (OUT1)
Moteur + 2: J3.6, U2.1 (OUT1)
Moteur - 1: J1.1, U1.7 (OUT2)
Moteur - 2: J3.1, U2.7 (OUT2)
NRST: C12.1, J9.12 (~RST), SW1.1 (A), U3.7 (PG10)
unnamed: C23.1, R12.2
unnamed: C24.1, R13.1, R14.1, R15.1
unnamed: D2.2 (A), R5.2
unnamed: D3.2 (A), R6.2
unnamed: D4.2 (A), R7.2
unnamed: J8.2, SW2.2
unnamed: MP1.5 (BST), R12.1
unnamed: MP1.6 (EN/SYNC), R10.2
unnamed: MP1.8 (FB), R13.2
unnamed: C23.2, L2.1, MP1.3 (SW)
unnamed: C21.1, MP1.7 (VCC), R11.1
PG_51: MP1.1 (PG), R11.2, U3.2 (PC13)
PWM FWD 1: PWM FWD 1.1, U1.4 (FWD), U3.62 (PB9)
PWM FWD 2: PWM FWD 2.1, U2.4 (FWD), U3.60 (PB7)
PWM REV 1: PWM REV 1.1, U1.5 (REV), U3.61 (PB8)
PWM REV 2: PWM REV 2.1, U2.5 (REV), U3.59 (PB6)
PWM_LED1: J4.2, U3.57 (PB4)
SCL TOF: J10.3, J11.3, J12.3, J13.3, J14.3, J15.3, R9.2, U3.40 (PC8)
SDA TOF: J10.4, J11.4, J12.4, J13.4, J14.4, J15.4, R8.2, U3.41 (PC9)
SWCLK: J9.6 (JCLK/SWCLK), U3.50 (PA14)
SWDIO: J9.4 (JTMS/SWDIO), U3.49 (PA13)
UART_Debug_RX: J9.13 (VCP_RX), U3.53 (PC11)
UART_Debug_TX: J9.14 (VCP_TX), U3.52 (PC10)
UART_Pi_Zero_RX: J16.3, U3.17 (PA3)
UART_Pi_Zero_TX: J16.4, U3.14 (PA2)
UART_mp3_RX: J2.2, U3.55 (PD2)
UART_mp3_TX: J2.1, U3.54 (PC12)
XSHUT_1: J10.6, U3.21 (PA7)
XSHUT_2: J12.6, U3.24 (PB0)
XSHUT_3: J14.6, U3.23 (PC5)
XSHUT_4: J11.6, U3.26 (PB2)
XSHUT_5: J13.6, U3.33 (PB11)
XSHUT_6: J15.6, U3.19 (PA5)

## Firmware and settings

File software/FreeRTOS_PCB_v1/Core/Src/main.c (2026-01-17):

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
/* Includes ------------------------------------------------------------------*/
#include "main.h"
#include "cmsis_os.h"
#include "adc.h"
#include "dma.h"
#include "i2c.h"
#include "tim.h"
#include "usart.h"
#include "gpio.h"

/* USER CODE BEGIN Includes */
#include "tof.h"
#include "vl53l0x_api.h"
#include "vl53l0x_device.h"
#include <stdio.h>
#include "motors.h"
#include "lidar.h"
#include "brillez.h"
/* USER CODE END Includes */


void SystemClock_Config(void);
void MX_FREERTOS_Init(void);
/* USER CODE BEGIN 0 */
int __io_putchar(int ch) {
	HAL_UART_Transmit(&huart4, (uint8_t *)&ch, 1, HAL_MAX_DELAY);
	return ch;
}

static TaskHandle_t MotorTaskHandle;
static TaskHandle_t TOFTaskHandle;
SemaphoreHandle_t semMotorEnable;

void task_motors(void * unused){
  while(1){
    xSemaphoreTake(semMotorEnable, portMAX_DELAY);
    motor_forward(60, 'R', 0);
    motor_forward(50, 'L', 0);    
    vTaskDelay(pdMS_TO_TICKS(50)); 
  }
}

void task_tofs(void *unused){
  while (1){
    bool obstacle = false;

    for (uint8_t i = 0; i < 6; i++){
      if (VL53L0X_IsAboveThreshold(i)){
        obstacle = true;
        break;
      }
    }

    if (obstacle){
      xSemaphoreTake(semMotorEnable, 0);

      motors_stop_all();

      motor_backward(60, 'R', 0);
      motor_backward(50, 'L', 0);
      vTaskDelay(pdMS_TO_TICKS(1200));

      motors_stop_all();

      motor_turn(40, 60, 'F', 0);
      vTaskDelay(pdMS_TO_TICKS(500));
    }
    else{
      xSemaphoreGive(semMotorEnable);
    }

    vTaskDelay(pdMS_TO_TICKS(50));
  }
}


/* USER CODE END 0 */

/**
  * @brief  The application entry point.
  * @retval int
  */
int main(void)
{

  /* MCU Configuration--------------------------------------------------------*/

  /* Reset of all peripherals, Initializes the Flash interface and the Systick. */
  HAL_Init();

  /* Configure the system clock */
  SystemClock_Config();

  /* Initialize all configured peripherals */
  MX_GPIO_Init();
  MX_DMA_Init();
  MX_ADC1_Init();
  MX_I2C3_Init();
  MX_TIM1_Init();
  MX_TIM3_Init();
  MX_TIM4_Init();
  MX_TIM8_Init();
  MX_TIM16_Init();
  MX_UART4_Init();
  MX_UART5_Init();
  MX_USART2_UART_Init();
  MX_TIM5_Init();
  /* USER CODE BEGIN 2 */

  printf("TEST 12\r\n");
  HAL_TIM_PWM_Start(&htim5, TIM_CHANNEL_4); 
  __HAL_TIM_SET_COMPARE(&htim5, TIM_CHANNEL_4, 0); 


	printf("TEST TOFs\r\n");
	VL53L0X_InitAllSensor();
  printf("TEST MOTORS left 53\r\n");
  motors_init();
  printf("TEST LEDS\r\n");
  printf("LEDS INITIALIZED\r\n");
  printf("MOTORS INITIALIZED\r\n");
  printf("WAITING 5 SEC\r\n");
  HAL_Delay(500); 
  printf("STARTING TESTS\r\n");
  

    semMotorEnable = xSemaphoreCreateBinary();
    if (semMotorEnable == NULL) {
      while(1);
    }
    xSemaphoreGive(semMotorEnable);


  if (xTaskCreate(task_motors, "MOTORS", 256, NULL, 3, &MotorTaskHandle) != pdPASS){
		printf("Error creating task b1");
		Error_Handler();
	}
  else{
    printf("Motor task created\r\n");
  }

  if(xTaskCreate(task_tofs, "TOFS", 512, NULL, 2, &TOFTaskHandle) != pdPASS){
    printf("Error creating task test tofs");
    Error_Handler();
  }
  else{
    printf("TOF task created\r\n");
  }


  vTaskStartScheduler();

  /* USER CODE END 2 */

  /* Call init function for freertos objects (in cmsis_os2.c) */
  MX_FREERTOS_Init();

  /* Start scheduler */
  osKernelStart();

  /* We should never get here as control is now taken by the scheduler */

  /* Infinite loop */
  /* USER CODE BEGIN WHILE */
	while (1) 
	{


    // motor_forward(40, 'R');
    // HAL_Delay(5000);
    // motor_stop_right();
    // HAL_Delay(5000);

// #################################### TOF
		// VL53L0X_IsAboveThreshold(0);
    // HAL_Delay(1000);
    // VL53L0X_IsAboveThreshold(1);
    // HAL_Delay(1000);
    // VL53L0X_IsAboveThreshold(2);
    // HAL_Delay(1000);
    // VL53L0X_IsAboveThreshold(3);
    // HAL_Delay(1000);
    // VL53L0X_IsAboveThreshold(4);
    // HAL_Delay(1000);
    // VL53L0X_IsAboveThreshold(5);
    // HAL_Delay(1000);
// #################################### TOF

// #################################### MOTORS

    // motor_forward(60, 'R');
    // // motor_forward(20, 'L');
    // HAL_Delay(5000);
    // motor_backward(40, 'R');
    // // motor_backward(80,'L');
    // HAL_Delay(3000);
// #################################### MOTORS



    /* USER CODE END WHILE */

    /* USER CODE BEGIN 3 */
	}
  /* USER CODE END 3 */
}

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


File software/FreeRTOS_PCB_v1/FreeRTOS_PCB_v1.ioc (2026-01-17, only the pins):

Mcu.UserName=STM32G474RETx
PA1.GPIO_Label=ADC_bat
PA1.Signal=ADC1_IN2
PA13.Signal=SYS_JTMS-SWDIO
PA14.Signal=SYS_JTCK-SWCLK
PA2.GPIO_Label=UART_LIDAR
PA2.Signal=USART2_TX
PA3.GPIO_Label=M_CTRL
PA3.Signal=S_TIM5_CH4
PA4.GPIO_Label=INT1
PA4.Signal=GPXTI4
PA5.GPIO_Label=XSHUT1
PA5.Signal=GPIO_Output
PA6.GPIO_Label=INT2
PA6.Signal=GPXTI6
PA7.GPIO_Label=XSHUT2
PA7.Signal=GPIO_Output
PB0.GPIO_Label=XSHUT4
PB0.Signal=GPIO_Output
PB1.GPIO_Label=INT4
PB1.Signal=GPXTI1
PB10.GPIO_Label=INT0
PB10.Signal=GPIO_Output
PB11.GPIO_Label=XSHUT5
PB11.Signal=GPIO_Output
PB12.GPIO_Label=INT5
PB12.Signal=GPXTI12
PB2.GPIO_Label=XSHUT0
PB2.Signal=GPIO_Output
PB4.GPIO_Label=PWM_LED
PB4.Signal=S_TIM16_CH1
PB6.GPIO_Label=REV2
PB6.Signal=S_TIM4_CH1
PB7.GPIO_Label=FWD2
PB7.Signal=S_TIM4_CH2
PB8-BOOT0.GPIO_Label=REV1
PB8-BOOT0.Signal=S_TIM8_CH2
PB9.GPIO_Label=FWD1
PB9.Signal=S_TIM8_CH3
PC0.GPIO_Label=Encodeur1_PhaseB
PC0.Signal=S_TIM1_CH1
PC1.GPIO_Label=Encodeur1_PhaseA
PC1.Signal=S_TIM1_CH2
PC10.GPIO_Label=UART_ST-LINK_TX
PC10.Signal=UART4_TX
PC11.GPIO_Label=UART_ST-LINK_RX
PC11.Signal=UART4_RX
PC12.GPIO_Label=UART_MP3_TX
PC12.Signal=UART5_TX
PC4.GPIO_Label=INT3
PC4.Signal=GPIO_Output
PC5.GPIO_Label=XSHUT3
PC5.Signal=GPIO_Output
PC6.GPIO_Label=Encodeur2_PhaseA
PC6.Signal=S_TIM3_CH1
PC7.GPIO_Label=Encoder2_PhaseB
PC7.Signal=S_TIM3_CH2
PC8.GPIO_Label=I2C_TOF_SCL
PC8.Signal=I2C3_SCL
PC9.GPIO_Label=I2C_TOF_SDA
PC9.Signal=I2C3_SDA
PD2.GPIO_Label=UART_MP3_RX
PD2.Signal=UART5_RX
PG10-NRST.GPIO_Label=NRST
PG10-NRST.Signal=GPXTI10

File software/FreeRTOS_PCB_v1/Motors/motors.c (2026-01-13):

// /*
//   Created by Vincent Fernandes, 06 December 2025.
//   This file is part of the Robot-chat project.
//  */

// #include "motors.h"

// Motors right_motor ={
//   .timer = &htim8,
//   .channel = TIM_CHANNEL_3,
//   .speed = 0,
//   .direction = 'F'
// };

// Motors left_motor ={
//   .timer = &htim4,
//   .channel = TIM_CHANNEL_2,
//   .speed = 0,
//   .direction = 'F'
// };

// PID pid_right = {
//   .Kd = 0,
//   .Kp = 0, 
//   .Ki = 0,
//   .error = 0,
//   .prev_error = 0,
//   .sum_error = 0,
//   .diff_error = 0
// };

// PID pid_left = {
//   .Kd = 0,
//   .Kp = 0, 
//   .Ki = 0,
//   .error = 0,
//   .prev_error = 0,
//   .sum_error = 0,
//   .diff_error = 0
// };

// Robot robot = {
//   .right_motor = &right_motor,
//   .left_motor = &left_motor,
//   .right_pid = &pid_right,
//   .left_pid = &pid_left
// };



// void motor_right_start_fwd(void){
//     HAL_TIM_PWM_Start(robot.right_motor->timer, robot.right_motor->channel);
// }
// void motor_right_start_rev(){
//     HAL_TIMEx_PWMN_Start(robot.right_motor->timer, robot.right_motor->channel);
// }
// void motor_left_start_fwd(void){
//     HAL_TIM_PWM_Start(robot.left_motor->timer, robot.left_motor->channel);
// } 
// void motor_left_start_rev(){
//     HAL_TIMEx_PWMN_Start(robot.left_motor->timer, robot.left_motor->channel);
// }
// void motor_right_stop_fwd(void){
//     HAL_TIM_PWM_Stop(robot.right_motor->timer, robot.right_motor->channel);
// }
// void motor_right_stop_rev(void){
//     HAL_TIMEx_PWMN_Stop(robot.right_motor->timer, robot.right_motor->channel);
// }
// void motor_left_stop_fwd(void){
//     HAL_TIM_PWM_Stop(robot.left_motor->timer, robot.left_motor->channel);
// }
// void motor_left_stop_rev(void){
//       HAL_TIMEx_PWMN_Stop(robot.left_motor->timer, robot.left_motor->channel);
// }

// // TODO : Change parameters in motors movements in order to use speed in "m/s, motor_id, time" as parameters
// // TODO : Make some others functions like ramp up or ramp down to accelerate and decelerate.
// // TODO : maybe put PID structures inside motors instead of robot 
// void motors_init(void){

//   motor_right_start_fwd();
//   motor_right_start_rev();
//   motor_left_start_fwd();
//   motor_left_start_rev();

// 	__HAL_TIM_MOE_ENABLE(robot.right_motor->timer);
//   __HAL_TIM_MOE_ENABLE(robot.left_motor->timer);

// 	__HAL_TIM_SET_COMPARE(robot.right_motor->timer, robot.right_motor->channel, 0);
// 	__HAL_TIM_SET_COMPARE(robot.left_motor->timer, robot.left_motor->channel, 0);
// }

// void motors_stop_all(){
//   __HAL_TIM_SET_COMPARE(robot.right_motor->timer, robot.right_motor->channel, 0);
// 	__HAL_TIM_SET_COMPARE(robot.left_motor->timer, robot.left_motor->channel, 0);

//   motor_right_stop_fwd();
//   motor_right_stop_rev();
//   motor_left_stop_fwd();
//   motor_left_stop_rev();
// }


// void motor_forward(uint8_t speed_percent, char motor_id){
//     uint32_t duty  = motor_set_speed(speed_percent, motor_id);
//     if(motor_id == 'R'){
//       motor_right_start_fwd();
//       motor_right_stop_rev();
//       __HAL_TIM_SET_COMPARE(robot.right_motor->timer, robot.right_motor->channel, duty);
//     }
//     else if (motor_id == 'L'){
//       motor_left_start_fwd();
//       motor_left_stop_rev();
//       __HAL_TIM_SET_COMPARE(robot.left_motor->timer, robot.left_motor->channel, duty);
//     }
// }

// void motor_backward(uint8_t speed_percent, char motor_id){
//     uint32_t duty  = motor_set_speed(speed_percent, motor_id);
//     if(motor_id == 'R'){
//       motor_right_start_rev();
//       motor_right_stop_fwd();
//       __HAL_TIM_SET_COMPARE(robot.right_motor->timer, robot.right_motor->channel, duty);
//     }
//     else if (motor_id == 'L'){
//       motor_left_start_rev();
//       motor_left_stop_fwd();
//       __HAL_TIM_SET_COMPARE(robot.left_motor->timer, robot.left_motor->channel, duty);
//     }
// }

// void motor_turn(uint8_t speed_right, uint8_t speed_left, char direction){
//     uint32_t duty_right  = motor_set_speed(speed_right, 'R');
//     uint32_t duty_left  = motor_set_speed(speed_left, 'L');
//     if(direction == 'F'){
//       motor_forward(duty_right, 'R');
//       motor_forward(duty_left, 'L');
//     }
//     else if(direction == 'B'){
//       motor_backward(duty_right, 'R');
//       motor_backward(duty_left, 'L');     
//     }
//     else{
//       printf("Direction is not valid\r\n");
//     }
// }

// uint32_t motor_set_speed(uint8_t speed_percent, char motor_id){
//     if(speed_percent > 100){
//         speed_percent = 100;
//     }
//     else if (speed_percent < 30)
//     {
//         speed_percent = 30;
//     }

//     if(motor_id == 'R'){
//         uint32_t duty = (robot.right_motor->timer->Init.Period * speed_percent) / 100;
//         return duty;
//     }
//     else if(motor_id == 'L'){
//         uint32_t duty = (robot.left_motor->timer->Init.Period * speed_percent) / 100;
//         return duty;
//     }
//   return 0;
// }

// //////////////////////////////////////////////////////////////////////////////////////
// /*Encoder Part*/
// //////////////////////////////////////////////////////////////////////////////////////
// /*TODO : Test PID to have values for Kd, Kp, Ki. Probably using a PI instead of a PID
// make a table to register all real speed values for a given time to check how the PID is working*/

// void start_encoder(){
//   HAL_TIM_Encoder_Start(&htim3, TIM_CHANNEL_ALL);

// }

// #define CPR 224.4f   

// int32_t prev_pos = 0;
// const float dt = 0.01f;

// float get_real_rpm(void){
//     int32_t pres_pos = (int32_t)__HAL_TIM_GET_COUNTER(&htim3);
    

//     int32_t delta = pres_pos - prev_pos;

//     if(delta < 0){
//       printf("Going Backward\r\n");
//     }
//     else if(delta > 0){
//       printf("Going Forward \r\n");
//     }
//     else{
//       printf("Motor Stopped\r\n");
//     }

//     prev_pos = pres_pos;

//     float cps = delta / dt;
//     float rpm = (cps / CPR) * 60.0f;

//     return rpm;
// }

// // int past_error_right = 0;
// // int sum_error_right = 0;
// // int past_error_left = 0;
// // int sum_error_left = 0;

// // void compute_pid(uint8_t speed_th, float speed_real, char motor_id){
// //     if (motor_id == 'R'){
// //       int Kd = robot.right_pid->Kd;
// //       int Ki = robot.right_pid->Ki;
// //       int Kp = robot.right_pid->Kp;
// //     }

// // }

// uint8_t compute_pid_right(uint8_t speed_th, float speed_real){
//     uint8_t pid_out = 0; 
//     uint8_t speed_PWM = 0;
//     robot.right_pid->error = speed_th - speed_real;
//     pid_out += robot.right_pid->Kp* robot.right_pid->error;

//     robot.right_pid->sum_error += robot.right_pid->error *dt;
//     pid_out += robot.right_pid->Ki * robot.right_pid->sum_error;

//     robot.right_pid->diff_error = (robot.right_pid->error - robot.right_pid->prev_error)/dt;
//     pid_out += robot.right_pid->Kd * robot.right_pid->diff_error;
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

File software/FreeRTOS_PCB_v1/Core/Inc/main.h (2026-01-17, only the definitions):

#define NRST_Pin GPIO_PIN_10
#define NRST_GPIO_Port GPIOG
#define NRST_EXTI_IRQn EXTI15_10_IRQn
#define Encodeur1_PhaseB_Pin GPIO_PIN_0
#define Encodeur1_PhaseB_GPIO_Port GPIOC
#define Encodeur1_PhaseA_Pin GPIO_PIN_1
#define Encodeur1_PhaseA_GPIO_Port GPIOC
#define ADC_bat_Pin GPIO_PIN_1
#define ADC_bat_GPIO_Port GPIOA
#define UART_LIDAR_Pin GPIO_PIN_2
#define UART_LIDAR_GPIO_Port GPIOA
#define M_CTRL_Pin GPIO_PIN_3
#define M_CTRL_GPIO_Port GPIOA
#define INT1_Pin GPIO_PIN_4
#define INT1_GPIO_Port GPIOA
#define INT1_EXTI_IRQn EXTI4_IRQn
#define XSHUT1_Pin GPIO_PIN_5
#define XSHUT1_GPIO_Port GPIOA
#define INT2_Pin GPIO_PIN_6
#define INT2_GPIO_Port GPIOA
#define INT2_EXTI_IRQn EXTI9_5_IRQn
#define XSHUT2_Pin GPIO_PIN_7
#define XSHUT2_GPIO_Port GPIOA
#define INT3_Pin GPIO_PIN_4
#define INT3_GPIO_Port GPIOC
#define XSHUT3_Pin GPIO_PIN_5
#define XSHUT3_GPIO_Port GPIOC
#define XSHUT4_Pin GPIO_PIN_0
#define XSHUT4_GPIO_Port GPIOB
#define INT4_Pin GPIO_PIN_1
#define INT4_GPIO_Port GPIOB
#define INT4_EXTI_IRQn EXTI1_IRQn
#define XSHUT0_Pin GPIO_PIN_2
#define XSHUT0_GPIO_Port GPIOB
#define INT0_Pin GPIO_PIN_10
#define INT0_GPIO_Port GPIOB
#define XSHUT5_Pin GPIO_PIN_11
#define XSHUT5_GPIO_Port GPIOB
#define INT5_Pin GPIO_PIN_12
#define INT5_GPIO_Port GPIOB
#define INT5_EXTI_IRQn EXTI15_10_IRQn
#define Encodeur2_PhaseA_Pin GPIO_PIN_6
#define Encodeur2_PhaseA_GPIO_Port GPIOC
#define Encoder2_PhaseB_Pin GPIO_PIN_7
#define Encoder2_PhaseB_GPIO_Port GPIOC
#define I2C_TOF_SCL_Pin GPIO_PIN_8
#define I2C_TOF_SCL_GPIO_Port GPIOC
#define I2C_TOF_SDA_Pin GPIO_PIN_9
#define I2C_TOF_SDA_GPIO_Port GPIOC
#define UART_ST_LINK_TX_Pin GPIO_PIN_10
#define UART_ST_LINK_TX_GPIO_Port GPIOC
#define UART_ST_LINK_RX_Pin GPIO_PIN_11
#define UART_ST_LINK_RX_GPIO_Port GPIOC
#define UART_MP3_TX_Pin GPIO_PIN_12
#define UART_MP3_TX_GPIO_Port GPIOC
#define UART_MP3_RX_Pin GPIO_PIN_2
#define UART_MP3_RX_GPIO_Port GPIOD
#define PWM_LED_Pin GPIO_PIN_4
#define PWM_LED_GPIO_Port GPIOB
#define REV2_Pin GPIO_PIN_6
#define REV2_GPIO_Port GPIOB
#define FWD2_Pin GPIO_PIN_7
#define FWD2_GPIO_Port GPIOB
#define REV1_Pin GPIO_PIN_8
#define REV1_GPIO_Port GPIOB
#define FWD1_Pin GPIO_PIN_9
#define FWD1_GPIO_Port GPIOB

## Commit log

2025-09-10 schematic pcb v0
    [PCB projet ESE.kicad_sch]
2025-09-11 kicad moteurs
2025-09-11 maj schematic
    [PCB projet ESE.kicad_sch]
2025-09-12 Kicad for Reg Values
    [Reg_values.kicad_pcb, Reg_values.kicad_sch]
2025-09-12 pcb schematic maj
    [PCB projet ESE.kicad_sch, Rasbpi.kicad_sch, Régulateurs.kicad_sch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]
2025-09-14 finish first version of schematic
    [PCB projet ESE.kicad_pcb, PCB projet ESE.kicad_sch, Rasbpi.kicad_sch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]
2025-09-15 maj scgematic
    [PCB projet ESE.kicad_sch]
2025-09-15 maj schematic & pinout CubeIDE
    [BOM_ESE_1.csv, PCB projet ESE.csv, PCB projet ESE.kicad_pcb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]
2025-09-15 maj schematic et pinout
    [PCB projet ESE.kicad_pcb, PCB projet ESE.kicad_sch]
2025-09-16 First Onshape Draft
    [RapidModelofComp.stl, Raspberry_Pi_4B_Copy.stl]
2025-09-16 update pcb
    [PCB projet ESE.kicad_pcb, PCB projet ESE.kicad_sch, TOF.kicad_sch]
2025-09-17 modif pcb editor & sch for new uc pinout
    [BOM_ESE_1.csv, PCB projet ESE.kicad_pcb, PCB projet ESE.kicad_sch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]
2025-09-17 replace usb c by jst xh
    [PCB projet ESE.kicad_pcb, PCB projet ESE.kicad_sch, Rasbpi.kicad_sch]
2025-09-18 v1 PCB
    [PCB projet ESE.kicad_pcb, PCB projet ESE.kicad_sch, Rasbpi.kicad_sch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]
2025-09-22 maj pcb and pinout
    [BOM_ESE_1.csv, PCB projet ESE.csv, PCB projet ESE.kicad_pcb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]
2025-09-22 Create PCB projet ESE-2025-09-22_171303.zip
2025-09-24 maj inductance 4.7uH
    [PCB projet ESE.kicad_pcb, Régulateurs.kicad_sch]
2025-09-25 maj C25 & C26
    [PCB projet ESE.kicad_pcb, Régulateurs.kicad_sch]
2025-09-26 maj mpn & gitignore
    [PCB projet ESE.kicad_sch]
2025-09-26 maj datasheet
    [PCB projet ESE.kicad_pcb, PCB projet ESE.kicad_sch, PCB projet ESE2.csv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]
2025-09-26 maj pinout pcb 2425
2025-09-28 modelisation v1
    [Part 1.3mf, Part 1.stl, Part 2.stl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]
2025-09-30 v2 meca
    [Part 2:3:4:5:6:9:R.3mf, Part1_v2.3mf, Part5_v2.3mf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]
2025-09-30 Start for motor
2025-10-01 review pcb
    [PCB projet ESE.kicad_pcb, PCB projet ESE.kicad_sch]
2025-10-01 lidar avec nucleo premier code avec reception uart à interruption ligne IDLE
2025-10-01 started code for motor
2025-10-03 LED NEOPIXEL
2025-10-06 tof & led v2
2025-10-06 onshape v4
    [LED.3mf, Li-ion_cache.3mf, Part1_v4.stl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]
2025-10-07 avec les commentaires ajoutés
2025-10-09 code Lidar v2
2025-10-12 uart js code
2025-10-12 add print connect
2025-10-13 print JSON in Rasbpi
2025-10-13 Continuing on motors
2025-10-20 add BOM with M POMMERY plug-in
2025-11-06 test vscode/stm32CubeIDE
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2025-11-08 schematic PCB ampli
    [PCB_AMPLI.kicad_pcb, PCB_AMPLI.kicad_sch]
2025-11-08 sch v2 ampli
    [PCB_AMPLI.kicad_pcb, PCB_AMPLI.kicad_sch]
2025-11-08 pcb ampli final 1.0
    [PCB_AMPLI.kicad_pcb, PCB_AMPLI.kicad_sch]
2025-11-09 gerbers pcb ampli
    [PCB_AMPLI-B_Cu.gbr, PCB_AMPLI-B_Mask.gbr, PCB_AMPLI-B_Paste.gbr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]
2025-11-09 forgotten MPN and doc
    [PCB_AMPLI.kicad_sch]
2025-11-09 fix width
    [PCB_AMPLI.kicad_pcb]
2025-11-10 BOM Ampli
    [PCB_AMPLI_BOM.csv]
2025-11-12 avec fonciton de detection de cible
2025-11-17 Li-Ionholder v1
    [Li-ion 1S.stl]
2025-11-18 fix : free le malloc et du coup ca s'arrete plus au bout de quelques minute
    [lidar.c, main.c]
2025-11-18 Pinout Cube MX v1 for PCB v2
    [PCB_Projet_ESE_v2.kicad_pcb, PCB_Projet_ESE_v2.kicad_sch, Régulateurs.kicad_sch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]
2025-11-19 fix le probleme de continuite au niveau 0 degre et 360 degre
    [lidar.c, lidar.h]
2025-11-19 Finished Pinout v2
    [PCB_Projet_ESE_v2.kicad_sch]
2025-11-20 Schematic done for PCB v2
    [PCB_Projet_ESE_v2.kicad_pcb, PCB_Projet_ESE_v2.kicad_sch, Régulateurs.kicad_sch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]
2025-11-21 first version 52*52mm
    [PCB_Projet_ESE_v2.kicad_pcb, PCB_Projet_ESE_v2.kicad_sch]
2025-11-22 new version 47x47mm
    [PCB_Projet_ESE_v2.kicad_pcb, PCB_Projet_ESE_v2.kicad_sch]
2025-11-25 routage en cours
    [Battery_Monitoring.kicad_sch, PCB_Projet_ESE_v2.kicad_pcb, PCB_Projet_ESE_v2.kicad_sch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]
2025-11-25 fix : lidar nucleo amélioration
    [lidar.c, lidar.h, main.c]
2025-11-26 TOF polling
    [Battery_Monitoring.kicad_sch, PCB_Projet_ESE_v2.kicad_pcb, PCB_Projet_ESE_v2.kicad_sch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]
2025-11-26 v1.5 PCB finished
    [PCB projet ESE.kicad_pcb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]
2025-12-02 PCB V2 routage v2 finished
    [Battery_Monitoring.kicad_sch, PCB_Projet_ESE_v2.kicad_pcb, PCB_Projet_ESE_v2.kicad_sch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]
2025-12-03 ordered PCB v2
    [Battery_Monitoring.kicad_sch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]
2025-12-03 tof2_nucleo, code pour les nouveaux tof, avec interruption sur seuil
2025-12-03 accel + motor test
2025-12-08 trying to comput pid
2025-12-09 code tof avec interruption et plusieurs tof
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2025-12-10 lecture d'acceleration en interruption
2025-12-11 TOF working polling
    [TEST_TOF_2 Debug.cfg]
2025-12-16 accelerometre interruption sur single tap
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2025-12-16 test lidar and TOF ok
2025-12-25 better version of Lidar code and begin objects detection
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2026-01-14 FreeRTOS for Lidar and Tofs
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2026-01-15 remove accelerometre project parce que ca ne fonctionnait pas avec le premier pcb, du coup utiliser le driver de acc_test!!
2026-01-20 Add software report
    This document provides an overview of the software directory, detailing various tests and configurations related to STM32 projects, including accelerometer setup and LiDAR data processing.
2026-01-23 Fix spelling and clarity in README for TOF sensors
    Corrected spelling errors and improved clarity in the TOF sensor configuration section.
2026-01-25 Finish README
    [Battery_Monitoring.kicad_sch, Connectors.kicad_sch, Motors.kicad_sch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]
2026-01-26 j'ai remis le code tof_g747 parce que je l'aime bien mais j'ai expliqué qu'on l'a pas utilisé au finale dans le readme

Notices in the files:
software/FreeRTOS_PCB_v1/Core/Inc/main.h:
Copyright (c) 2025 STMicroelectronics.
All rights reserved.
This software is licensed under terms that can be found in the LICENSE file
